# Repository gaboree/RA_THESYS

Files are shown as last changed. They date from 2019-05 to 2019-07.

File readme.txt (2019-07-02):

This directory contains the documentation and software implementation of the Electromechanic rail model digitalization, based on ETCS principles.
The project was realised as Bachelor of Computer Science thesys.

To recreate the project, one needs to understand the documentation, and recreate the hardware components presented there.
With the correct hardware configuration, the code base found here can be used.

Folder: arduino_codes
Contains: implementation of: signal module, acc module, vacancy module, train module
	  tests of: sias algorithm,  register data split algorithm, vacancy module test, simple and duplex serial communication test, signal module test.

Folder: circuits
Contains: the images of the circuit diagrams, and also the source fzz files for each module.

Folder: procesing_codes
Contains: the UI implementation realized in Processing (Java), and the required images for the UI

Folder: document
Contains: the TEX code and used files structure in order to generate the PDF, using a TEX editor, added in zip format too.
	  the generated PDF of the documentation.

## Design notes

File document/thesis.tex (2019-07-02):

%!TeX spellcheck = hu_HU
\documentclass[a4paper,12pt]{article}
\include{preamble}

\author{Gábor Zsolt }
\title{Thesis Computer Science Railway model automated}
\clearcontents

\begin{document}

% Ro Front
\newpage
\pagestyle{empty}
\selectlanguage{romanian}
    \begin{center}
        {\Large Universitatea Sapientia din Cluj-Napoca}\\\vspace{0.07in}
		{\Large Facultatea de Științe Tehnice și Umaniste, Târgu-Mureș}\\\vspace{0.07in}
		{\Large Specializarea Calculatoare}\\
		
		\vspace{2.35in}
		
		{\huge Digitalizare unui model electromecanic }\\\vspace{0.15in}
		{\huge feroviar, bazată pe principii ETCS}
		
		\vspace{0.5in}
		
		{\LARGE Proiect de Diplomă }
		
	\end{center}
	
	\vspace{2.0in}
	
	\begin{multicols}{2}
		\begin{flushleft}
			{\Large Coordonator științific:}
		\end{flushleft}
		\columnbreak
		\begin{flushright}
			{\Large Absolvent:}
		\end{flushright}
	\end{multicols}
	\begin{multicols}{2}
		\begin{flushleft}
			{\LARGE Dr. Székely Sándor Endre}
		\end{flushleft}
		\columnbreak
		\begin{flushright}
			{\LARGE Gábor Zsolt}
		\end{flushright}
	\end{multicols}
	
	\vspace{1.5in}
		
	\begin{center}
		{\LARGE 2019}
	\end{center}
	
\newpage
\includepdf[pages=-]{Detalii_licenta_RO.pdf} 
\newpage
\includepdf[pages=-]{Declaratii_licenta_RO.pdf}
%Romanian abstract
\newpage
\includepdf[pages=-]{turnitin_report.pdf}

\newpage
\pagestyle{empty}
\begin{center}
		{\huge Digitalizare unui model electromecanic }\\\vspace{0.15in}
		{\huge feroviar, bazată pe principii ETCS}
	\vspace{0.1in}
	
    {\LARGE Extras}
\end{center}

Transportul feroviar în zilele noastre e o componentă organică al economiei și al transportului de masă.
Problema principală în tranzitul universal între diferite rețele ferate, este faptul că la nivel de țară sistemul de protecție al trenurilor diferă.
Pentru a soluționa această dificultate, prin UE, sa stabilit ERA (Agenția europeană de transport feroviar) care a dezvoltat sistemul universal ETCS.
Scopul lucrării mele de diplomă este de a integra aceste principii într-un model electromecanic de cale ferată. 
Bazând pe aceste principii sistemul are următoarele proprietăți: e o rețeaua închisă de 3 metrii, compus din căi ferate principale exclusiv, protecție de tren bazat pe un sistem de 8 blocuri, unidirecțional.
Modelul conține o locomotivă electromecanică, în care e integrat un motor de curent continuu pentru propulsie.
Arhitectura sistemului planificat și realizat conține cinci componente principale. 
Fiecare component hardware are în comun placa de dezvoltare Arduino NANO(utilizat pentru control) și modul de radio frecvență NRFL24 tip emisie-recepție (RFC - utilizat pentru transfer date între componente).
Primul, \textbf{controlul de tren}, prin modulare PWM regulează viteza trenului în 3 stări posibile. Semnalul de control vinde de prin RFC de la interfața grafică.
Adițional am instalat și două LEDuri în fața și spatele trenului, care au rol de input pentru sistemul de detectare.
Al doilea, \textbf{rețeaua de detectare}, e construit din 8 foto rezistoare, unul poziționat în fiecare bloc. LEDurile de pe tren activează senzorii și fiind legate de întrările analoage al Arduino, aceasta sunt transmise mai departe la controlul central.
Al treilea, \textbf{rețeaua de semnalizare}, controlează 3 circuite flip-flop pentru a activa o rețea de 8x3 LEDuri. Fiecare bloc are un semnalizator de trei leduri cu aspecte de culoare diferite ( ROȘU - Oprește, Verde - Înaintează, Galben - Atenție/Reduce Viteza).
Al patrulea, \textbf{controlul central}, numit și \textit{interlocking} în industrie, are rol de dealer între componente și garantarea condițiilor de siguranță. 
Pe baza datelor de detectare, prin algoritmul de secvențiere a aspectelor de semnal, determină aspectele de semnalizare de siguranță pentru fiecare bloc. Datele sunt transferate în continuu între el și celelalte componente.
În final, \textbf{interfața grafică}, compus din două părți, unul pentru controlul vitezei trenului, iar celălalt pentru afișarea stării rețelei de detectare și semnalizare. E rulat pe un calculator, și e în contact permanent prin USB, cu controlul central.
Hardwareul a fost programat în Arduino IDE, folosind limbajul C. Interfața a fost realizat cu Processing IDE, folosind limbajul Java.
După construcția și punerea în funcțiune, sistemul a fost testat cu succes cu unu și doi trenuri în rețeaua realizată. Concluzia fiind că e posibil să aplicăm sistemul ETCS pe modele ferate.
Cea mai importantă posibilitate de dezvoltare a sistemului actual ar însemna integrarea unor macaze. Acestea ar permite dezvoltarea rețelei cu căi secundare, și cu gări.
Care la rândul rol sunt condiționate de dezvoltarea controlului prin circulație bi-direcțională în rețea, și implementarea setării traseelor. 

\newpage
\section*{Cuprins}
	\begingroup
	\renewcommand{\section}[2]{}
	\romaniantableofcontents
	\endgroup

%Hungarian tehsys
\newpage
\pagestyle{empty}
\selectlanguage{hungarian}

	\begin{center}
		{\Large Sapientia Erdélyi Magyar Tudomány Egyetem}\\\vspace{0.07in}
		{\Large Marosvásárhelyi Kar}\\\vspace{0.07in}
		{\Large Számítástechnika szak}\\
		
		\vspace{2.35in}
		
		{\huge Elektromechanikus vasút modell }\\\vspace{0.15in}
		{\huge digitalizálása, ETCS elvekre alapozva}
		
		\vspace{0.5in}
		
		{\LARGE Diplomadolgozat}
		
	\end{center}
	
	\vspace{2.0in}
	
	\begin{multicols}{2}
		\begin{flushleft}
			{\Large Témavezető:}
		\end{flushleft}
		\columnbreak
		\begin{flushright}
			{\Large Végzős hallgató:}
		\end{flushright}
	\end{multicols}
	\begin{multicols}{2}
		\begin{flushleft}
			{\LARGE Dr. Székely Sándor Endre}
		\end{flushleft}
		\columnbreak
		\begin{flushright}
			{\LARGE Gábor Zsolt}
		\end{flushright}
	\end{multicols}
	\begin{flushleft}
		{\Large egyetemi adjunktus}
	\end{flushleft}
	\vspace{1.2 in}
		
	\begin{center}
		{\LARGE 2019}
	\end{center}
%Hungarian abstract
\newpage
\pagestyle{empty}
\begin{center}
    {\LARGE Kivonat}
\end{center}
\textbf{Kulcsszavak:} Vasúti modell, ECTS, Vasúti blokk, Jelzö aspektus, Arduino, Rádió frekvenciás kommunikáció.

A vasúti szállítás napjainkban a gazdaság és a tömegszállítás szerves része. Vasúti hálózatok országonként egymástól eltérő vonat védelmi technológiát alkalmaznak, szükségszerűen megalakult, az Európai Unió közvetlen hatására, az ETCS(European Train Control and Signalling). Ez a vasúti hálózatok vezérlésért felelős elvek összessége amelynek célja a vasúti forgalom zökkenőmentes működése ország határokon túl. A diplomamunkám témája, egy egyszerű elektromechanikus modell vasút digitalizálása, az ETCS elveket szem elött tartva. Konkrétan egy ETCS 2-es szintű, fővágányokból álló, zárt, egy irányú, nyílt szakaszú vasúti blokk rendszer szemi automatikus vezérlése. A modell egy három méter hosszú müanyag vágány pályát, és egy DC motorral meghajtótt mozdonyt tartalmazz.A pályát 8 darab vasúti blokkra osztottam.A megvalósított rendszer öt darab fő részre osztható.Mindegyiknek a közös hardver része egy Arduino NANO mikrokontroller (vezérlésért felelős) és egy NRFL24 rádió frekvenciás modul (komponensek közötti kommunikációért felelős). Első a \textbf{mozdony irányítás}. A mikrokontroller PWM modulációval, és egy tranzisztorral kapcsoló üzemmódban, tudja módosítani a mozdony sebességét. Rádió frekvencián keresztül irányítható a grafikus interfészről. Mozdonyra elejére és végére szerelt két LED jelzi az észlelő hálózati szenzornak a mozdony relatív pozícióját. Második az \textbf{ észlelő hálózat} 8 db. fotó-ellenállások által képviselt szenzorok bemenete analóg portokon. A mozdony LED-ekre reagál. Harmadik a \textbf{jelző hálózat} három darab shift regisztert vezérel, amelyek egy 8x3-as LED hálózatot aktiválnak. Mindegyik blokkhoz tartozik egy 3 LED-es jelző amelyek szín aspektusokat állítanak be (Piros - Állj, Sárga - Lassíts és figyelj, Zöld - Szabad a behajtás). Vizuális információ a mozdony vezető számára. Negyedik a \textbf{központi vezérlés} fogadja, feldolgozza, és továbbítja az adatokat a komponensnek között. Szaknyelven egy köztes réteget képvisel amelyet biztosító/óvó rendszernek is neveznek. USB porton keresztül, kapcsolatban van a számítógépen futó grafikus interfésszel. Az interfésztől fogadja a mozdony vezérlési adatokat amelyet továbbit a felelős komponensnek. Végül a \textbf{grafikus interfész} két részből áll. Mozdony vezérlése, három sebesség pozícióval: Állj, Maximális sebesség, Fél sebesség. És a hálózat topológia megjelenítése, a hozzá tartozó észlelési és jelző adatokkal. A rendszerben a komponensek NRFL24-es moduljai egymás között két irányú adat áramlásra képesek. A hardver szintű kód az Ardunio NANO és NRFL24 modul vezérlésére Arduino IDE környezetben íródott C programozási nyelvben. A grafikus interfész Processing fejlesztői környezetben íródott Java programozási nyelvben. A rendszer elkészítése, és összeszerelése után, a rendszert egy valamint két mozdony modullal teszteltem. Az említett rendszer sikeresen teljesítette a dolgozatban megfogalmazott követelményeket. Állíthatom hogy, leskálázott alap szinten, megfelel az ETCS előírásoknak. A rendszer legfontosabb továbbfejlesztési lehetősége a hálózat bővítése vasúti eltérítőkkel. Ez lehetőséget adna állomások, valamint két irányú vágányok integrálására. Az utóbbi pedig a vasúti blokk elv, komplementerére, a vasúti útvonalak megvalósítását tenné lehetővé.
%English abstract
\newpage
\pagestyle{empty}
\begin{center}
    {\LARGE Abstract}
\end{center}
\textbf{Keywords:} Rail model, ETCS, Rail block, Arudino, Radio frequency communication, Signal aspect.

Rail transport in our time is an organic component of the economy and mass transit services. 
The main issue in universal, standardized transit of rail vehicles across all networks, is that each country has adopted his own rules of train protection.
To solve this issue, through the EU, the ERA developed the ETCS (European Train Control and Signaling) set of rules.
This would allow ECTS compliant trains to transit across several ETCS networks belonging to different countries.
The goal of my thesis is to design and implement such a system, using an electro mechanic rail model.
Which will comply with ETCS level 2 rules and has the following properties: it's a 3 meter long loop like closed network, consists of main tracks only, protection based on block system in open line.
The network is broken up in to 8 rail blocks, and the train has a built in DC motor, that must be remote controlled.
So the basic architecture of our system will consist of five main components. In each components case the hardware is built around an Arduino Nano(responsible for control) development board, and a NRFL24 radio transmitter (RTS-responsible for bi-directional data transfer).
First the \textbf{train control} is realized by PWM modulation via the MCU, and the remote control function by the RTS. The input data is coming from a GUI. Additionally two LEDs are installed for train front and rear detection.
Second the \textbf{detection network} consists of 8 photo resistors, that detect the train LEDs, and forward the sensor data to the MCUs analog inputs. Which forwards it to central processing via the RTS.
Third the \textbf{signaling network} drives 3 shift registers, which drive a 8x3 network of LEDs. In each block we have a signal of three LEDs, that represent the speed aspect for the specific block (RED - STOP, GREEN -GO, YELLOW - SLOW).
The data for the activation is coming via RTS from the central component. Fourth \textbf{central control} collects the vacancy data and based on the signal aspect sequencing algorithm, calculates the correct signal aspect for each block. 
This module is considered the central layer, also called interlocking in the industry. Additionally it acts as a dealer, it sends and receives data between the hardware components and the GUI. 
Finally the \textbf{GUI}  consists of a 3 state train control interface and of a rail network state display. 
The hardware level software for the MCU control was written in Arduino IDE, in C language. 
The GUI was developed with Processing IDE, in Java language.
After building and commissioning, the system was successfully tested with one and two trains in the network.
The conclusion being that it is possible to apply ETCS rules on a rail model.
The most significant further development possibility of this system is the integration of point machines, which would allow beside the block system, the implementation of secondary tracks and route setting principle.	
\newpage
\section*{Tartalom}
\selectlanguage{hungarian}
	\begingroup
	\renewcommand{\section}[2]{}
	\tableofcontents
	\endgroup
	\begingroup
	\newpage
	\listoffigures
	\listoftables
	\lstlistoflistings
	\endgroup
\newpage
\pagestyle{fancy}
\rhead{\slshape \leftmark}
%1
\section{Bevezető}\sectionro{Introducere}
\subsection{Bevezető}\subsectionro{Introducere}
A vasúti szállítás volt az első verziója a mechanikus tömeg szállításnak, legyen szó személy vagy árú szállításról. 
A vasút feltalálása meglepően hosszú múltra tekint vissza. A vasút működési alap elvre hasonló szerkezetet, a történészek szerint, az ógörögök már i.e. 600-ban használták. 
A “Diolokos” egy 6-7 km hosszú mészkőből épített pálya volt, és szerepe hajók szállítása volt a Korintusi és a Szaróni öböl között.\cite{jwdrijvers92} 
A hajókat állatokkal húzták át egyik kikötőből a másikban, ezzel jelentősen csökkentve az utazási időt, különben napokban került volna a Peloponészosz félsziget megkerülése.
A következő népszerű vasúti alkalmazás a középkori bányákban használt fa pályákon, lovakkal vontatott, fa szerelvények. Német és angol lakta vidékeken volt gyakran alkalmazva.
Az igazi fordulópont a gőzmotor feltalálása volt az angol James Watt által, majd az ezt követő "gőz szekér" készítése 1804-ben.
A gőzhajtású mozdonyoknak felmérhetetlen szerepe volt a 18-19 században robbanás szerű ipari forradalomnak. Ezt a tendenciát majd később tovább növelte a dízel valamint elektromos motorok megjelenése a 20. században.
A vasút szerepe napjainkban felbecsülhetetlen befolyással bír.Hatalmas mennyiségű személy és árú szállításról ami vasúti hálózatok segítségével bonyolódik le. 
Vincent Baziet francia közgazdász tanulmánya \cite{vbazil13} szerint egy országnak a vasút hálózatának a hatékonysága szoros kapcsolatban áll azzal hogy mennyire fejelt és versenyképes maga az ország gazdasága.

\begin{figure}[htp]
    \centering
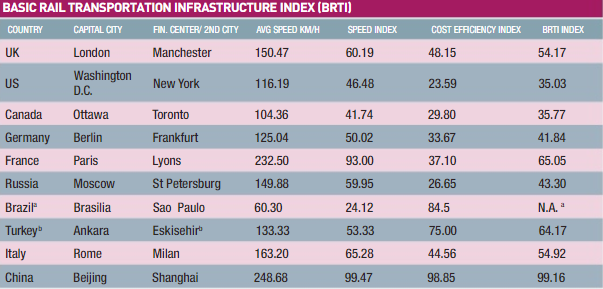
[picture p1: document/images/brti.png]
	
    \caption[Basic Rail Transportation Infrastructure Index]{BRT index}
	\label{fig:brti}
\end{figure}
    
Az általuk kiszámolt BRT index valóban alátámasztotta ezt, amint látható az \ref{fig:brti} ábrán, eredményeiket alátámasztja a stabil fejlődő gazdaságok igen csak magas indexel rendelkeznek.
Látható hogy gyengén fejlesztett vasút hálózatok esetén legtöbbször az index kiszámítása sem lehetséges. 
Tehát a globalizáció korszakában nyilvánvaló hogy a vasúti hálózatok jövője a fejlesztések folytatásával és ezen tudás megosztásával áll szoros kapcsolatban. 

\subsection{A dolgozat témája}\subsectionro{Tematica lucrării}
A dolgozatom témája egy modell vasúti hálózat automatizálásának megvalósítása. Tanulmányozva az iparban használt implementációs elveket, és ahol lehetséges ezekre az elvekre támaszkodva felépíteni a rendszert. Négy fontosabb részre oszthatjuk a rendszerünk amint látható a \ref{fig:realizedsys}. ábrán:
\begin{enumerate}
    \item A központi vezérlés: egy mikrokontroller figyel a hálózatban található többi mikrokontrollere és továbbítja egy számítógépre telepített vezérlő szoftvernek az érkező adatokat. A kommunikáció rádiófrekvencián történik és két irányú.
    \item A mozdony vezérlő: egy mikrokontroller segítségével megvalósítja a mozdonyban található DC motor sebesség vezérlését, valamint parancsokat fogad a központi vezérléstől.
    \item A jelző  hálózat: egy mikrokontroller segítségével megvalósítja a vasút rendszerekben használt jelző lámpák aspektusának a beállítását, a vezérlő adat ugyancsak rádiófrekvencián érkezik a központi vezérléstől.
    \item Az észlelő hálózat:  egy mikrokontroller segítségével megvalósítja a mozgásban levő szerelvény topológiai helyzetét, majd ezt az adatot továbbítja rádiófrekvencián keresztül a központi vezérlésnek.
\end{enumerate}

\begin{figure}[htp]
    \centering
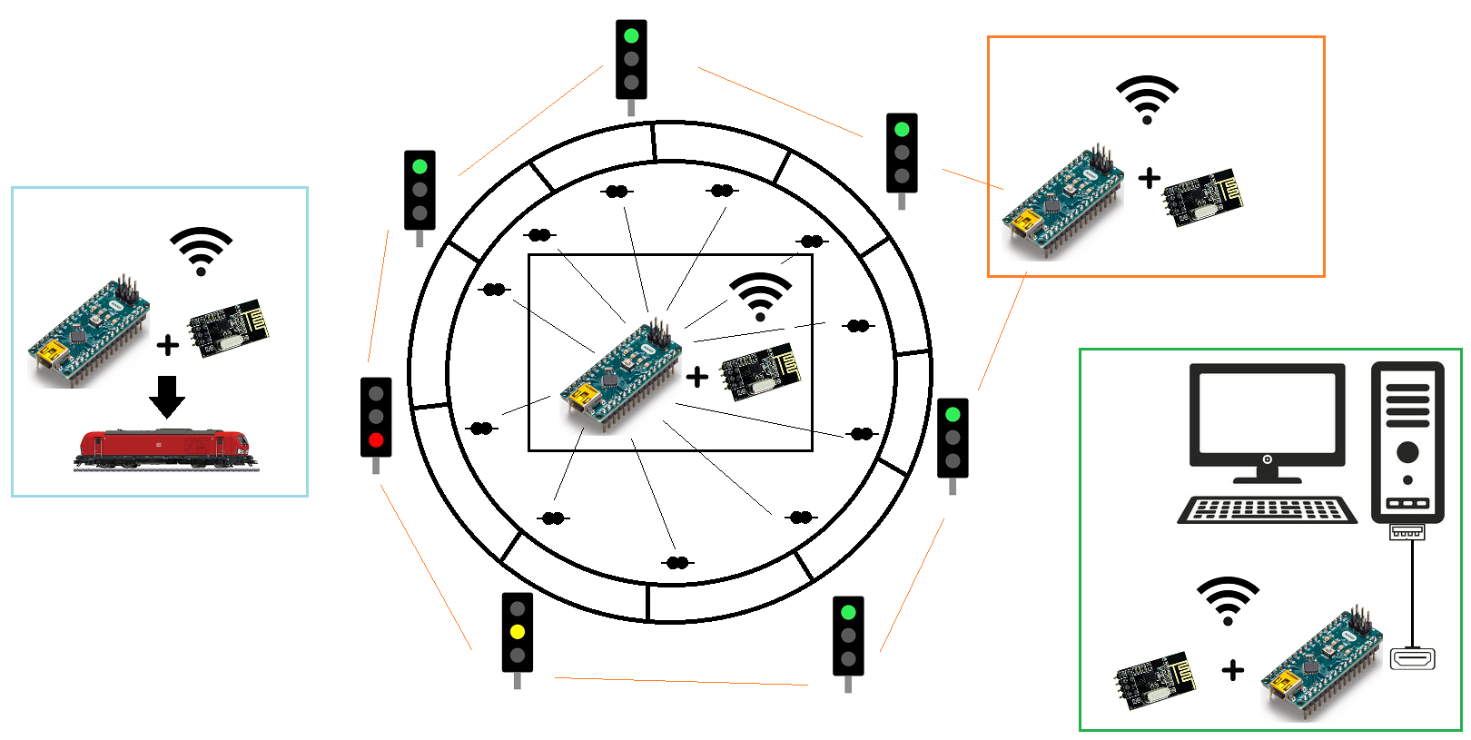
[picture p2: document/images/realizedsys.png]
	
    \caption[Megvalósított rendszer elvi rajz]{Megvalósított rendszer}
	\label{fig:realizedsys}
\end{figure}
%2
\section{Szakirodalmi tanulmány}\sectionro{Studiu bibliografic}\label{RAbasics}

A szakirodalmi tanulmány első sorban egy pár, a szakmában, nélkülözhetetlen könyvre épül.
A \textit {Joern Pachl: A vasúti üzemeltetés és ellenőrzés} \cite{jp09} és a \textit {Gregor Theeg, Sergej Vlasenko: Vasúti jelzés és biztosítóberendezések} \cite{gtsv18}, valamint a \textit{Peter Stanley: ETCS mérnököknek}\cite{ps11} című könyvek szinte kötelező irodalomként vannak számon tartva a vasúti elemek valamint logika fejlesztésének az ágazataiban. 
Értelemszerűen az elkövetkező fejezetek ezen könyvek tartalmának megemésztésével, újra fogalmazásával valamint magyar nyelvre való fordításával készültek el, kiegészítve a szakmában gyakran referált cikkekkel.

\subsection{Vasútrendszerek specifikációi}\subsectionro{Spețificațiile a sistemelor feroviare}
\textit {Jochen Trinckauf} szavait értelmezve az összes vasút rendszer esetében a következő két specifikációt azonosíthatjuk:
\begin{enumerate}
    \item A vonat által követet útvonalat a kerék és a sín mechanikai irányítása határozza meg, és ez az útvonal csak egy kitérő ( speciális vasúti elem) beavatkozásával változhat.
	Ebből kifolyólag lehetőség kell legyen egy ilyen rendszerben az útvonal beállításra, mivel a kitérők több lehetséges útvonalat megvalósítanak. Nyilvánvalóan egy vágányos rendszerek esetén, az irányváltoztatás zárt hurok használatával is megvalósítható. 
    Mivel a jármű szoros kapcsolatban áll az irányító rendszerrel, a vasúti rendszerek lineáris/szekvenciális rendszerekként is azonosíthatóak. 
	\item Az acél alapú vasúti kerekek relatív gyenge fékező képességgel rendelkeznek az ugyancsak acél alapú síneken. 
	Ebből kifolyólag a vezető által látható útvonalon kívül szükség van további elővigyázatossági intézkedésekre, annak érdekében hogy időben tudjon a vezető döntést hozni a sebesség csökkentésére vagy a vágány szakasz elhagyására vagy a teljes megállásra.
\end{enumerate}
\par Tehát ezekből azt a következtetés vonható le hogy, a vasúti rendszerekben esszenciális a helyes jelzés és vezérlés. 
A hálózat menedzser részéről fontos tudnia hogy egy adott időpontban pontosan hol, mikor és meddig van a gördülő állomány.
Annak érdekében hogy tudjon egy optimális és gazdaságos menetrendet szerkeszteni. 
Valamint a mozdony vezető - diszpécser - operátor szemszögéből fontosak ezek az elemek ahhoz hogy biztonságos, elérhető és karbantartott legyen a vasúti rendszer.
\pagebreak
\subsection{Vasúti elvek és standardok}\subsectionro{Principii și standarde feroviare}
Kibővítve a korábbi specifikációkat vasút rendszereknek három fontos részük van:
\begin{itemize}
	\item \underline{Infrastruktúra}, ami magában foglalja a teljes sin hálózatot/pályákat, állomásokat, és az ezekre szerelt mechanikus és/vagy elektromos felszerelést
	\item \underline{Gördülőállomány}, amely a mozdonyok és szerelvényeket képezi, fügétlenül attól hogy közszállítási vagy ipari szállításban használódik
	\item \underline{Üzemeltetési szabályok}, pontosabban a hálózatban használt működési szabályokat és eljárásosakat értjük ez alatt
\end{itemize}
\par Egyszerűség kedvéért az infrastruktúrát és gördülőállományt nevezhetjük a rendszer \textit{hardverének}, valamint az üzemeltetési szabályokat a \textit{szoftverének}.
Egy specifikus alrendszer az úgy nevezett automatikusa vonatvédelmi rendszer (\textbf{Automatic Train Protection}, továbbiakban \textbf{ATP}) felelős az egyik legfontosabb funkcióért a vasúti rendszerekben.
Az ATP szerepe az hogy információt továbbítson az útvonalról a mozdony vezetőhöz és automatikusan megállítsa a mozgó járművet ha emberi mulasztás miatt nem vesz figyelemben egy erre utaló jelzést a központi forgalom irányítótól. 
Ez az alrendszer tehát kapcsolatot teremt a gördülőállomány és az üzemeltetési szabályok között, információt szolgáltatva az infrastruktúrán található egyéb járművekről.
Feltalálása áttörő szerepet játszott a vasúti balesetek csökkentésében és/vagy szinte teljes elkerülésében. Sajnálatos módon az ATP rendszer implementációja nagyon nagy variációnak örvend.
Az európai országok közötti üzemeltetési szabályok annyira különbözőek voltak, hogy a 90-es évek végén több mint 14 különböző nemzeti standardot letehet azonosítani. 
Gyakorlatban szinte minden ország saját szabályokat alkalmaz, ennek az a negatív következménye hogy nagyon megnehezíti az átjárhatóságot az országok között. 
Az Európai Unió megalakulásának és idővel terjedésének köszönhetően, gazdasági okokból szükségszerű lett ezt a problémát megoldani. Mivel rengeteg idő és pénzügyi veszteséggel jár
minden országhatárnál mozdonyokat cserélni vagy készenlétben tartani határon túli szállítmányok esetén. Valamint ugyancsak magas költségel jár egy mozdony felszerelése több ország ilyen rendszerével.
Továbbá a nagy sebességű vonat hálózatok megjelenése, mint például a francia \underline{TGV}, a létező vezérlési technológiát is elavultnak tekintette.
Ezeknek következménye volt az \textbf{ERA - European Rail Agency} vagyis az \textit{Európai Vonat Ügynökség} megalakulása. 
Pár éven belül megalkották az átjárhatóságot lehetővé tevő technikai specifikációt, felkarolva az elődjét az \textbf{ERTMS - European Rail Traffic Management System}-et \textit{(Európai Vasút Forgalom Menedzsment Rendszer)}.
Az ERTMS komponenseként jött létre az \textbf{ETCS - European Train Control System}-et \textit{(Európai Vasút Vezérlési Rendszer)}.
Az ETCS szolgáltatja a technikai megoldásokat legtöbb új fejlesztésű vagy megújításra kerülő vasúti rendszereknek.
Idővel amint a megoldások bizonyították életképességüket,a kivitelezési folyamatot a \textbf{CENELEC} intézmény által standardizálták is.
\subsubsection{ETCS}\subsubsectionro{ETCS}
Az ETCS projekt célja hogy fokozatosan a hagyományos ATP rendszereket Európa szerte egy egységes két irányú kommunikációra képes vonat vezérlő rendszerre cserélje le.
Fontos megjegyezni hogy az újítás mindhárom vasút rendszeri komponenst érinti (Infrastruktúra, Gördülőállomány, Üzemeltetési szabályok).
Az új rendszerben új technológiákat vezettek be mint az \textbf{"euro-balise" (magyarul euró-pályamágnes)} vagy a GSM-R alapú kommunikáció. 
A pályamágnesek szerves részét képzik az ETCS technológiának, lényegében a sínek között elhelyezett jeladó szerkezet. 
Az az amikor egy ETCS rendszerrel felszerelt mozdony halad el fölötte információt továbbit a pályamágnes után következő útvonalról. Nagy előnye hogy statikus adat továbbítás esetén nem igényel külső áramforrást.
A kommunikáció típusától függően több szintre osztották az új megközelítéseket. 
Továbbiakban ezeket nézzük meg közelebbről.

\begin{itemize}
	\item \textit{0 szint} Ez a szint egy átmeneti állapotot ír le, az az eset amikor egy ETCS képes jármú egy non-ETCS hálózatban közlekedik.
	Egy ilyen szcenárióban a gördülőállomány maximum sebesség minimumával halad a hálózatban, és  emellett egy nemzetileg meghatározott 0 szintes sebesség korlátot is be kell tartania.	
	
	\item \textit{1 szint} Ezen a szinten az ATP egy fejlesztett időszakos verzióját találhatjuk és a pályamágnes az integrális fő adat átadási csatorna.
	Lényegében a pályamágnes, az érkező ETCS mozdonynak, mozgás engedélyt és profiladatokat továbbit.A pályamágnes lehet rögzített adat továbbító vagy váltható. 
	Míg az első csak statikus adatot továbbit ( például: földrajzi pozíció), addig  a második legtöbbször egy vonal menti elektromos készülék befolyására dinamikusan megválasztott adatot továbbit ( például: jelző aspektus).
	A pályamágnesek általában csoportokban vannak összekötve, így észlelhető ha valamelyik meghibásodik, valamint a csoport végső tagja képes információt továbbítani a következő csoport első tagjának.
	A csoportok közötti kommunikáció keretantennával bővülhet amely rádió frekvencián képes adatokat továbbítani, ezek az úgy nevezet Euroloop-ok.
	Érezhető hogy így relatív gazdaságosabban nagy távokat le tudnak fedni, lényeges vasút hálózat adatokat szolgáltatva.
	A harmadik lehetséges adat áramlás a helyváltoztatási adat, ezt az észlelő hálózat gyűjti be, az óvórendszer feldolgozza, és megfelelő jelző aspektust állít be, a biztonságos továbbhaladás érdekében.
	A járműn található ETCS berendezés ezen adatok alapján valós időben számol helyzetet, biztonsági féktávot, valamint egy sebességet amit közöl a vezetőnek.
	Ezt az elvi működést láthatjuk a \ref{fig:etcslevel1}. ábrán. Ez az alszinten valósítja meg a  teljes felügyelet módot. 
	Mivel az ETCS rendszer megszakítás nélkül felügyeli az összes befolyásoló paramétert.	
	\begin{figure}[htp]
	    \centering
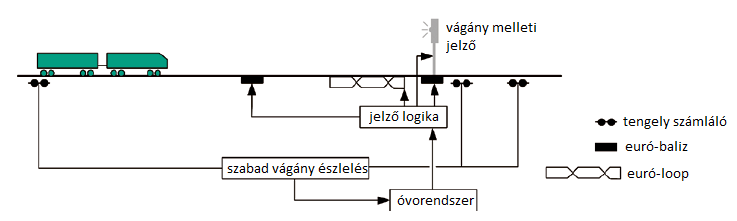
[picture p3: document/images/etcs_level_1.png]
	    
	    \caption[ETCS 1]{Adat folyam ETCS 1 szinten}
	    \label{fig:etcslevel1}
    \end{figure}
	
	Létezik viszont korlátozott felügyeleti mód is. Ez abban az esetben fordulhat elő, ha egy olyan jelző berendezéssel találkozik a jármű amely megállási aspektust mutat a vezetőnek.
	Ilyenkor egyéb ETCS rendszer nem szolgál más adattal, a vezető kénytelen ebben a módban megvárnia az aspektus változást ahhoz hogy tovább haladjon.
	
	\item \textit{2 szint} Egy folytonos ATP rendszerként működik. Ebben az esetben a vonat vezérlő adat GSM-R rádió frekvencián van továbbítva.
	A pályamágnesek továbbra is használtak, viszont döntő többségben statikus adatot szolgáltatnak az áthaladó szerelvénynek, szerepük elektromos vasúti mérföldköre hasonlítható.
	Adott egy adó vevő központ az RBC (Radio Block Center - Rádió Blokk Központ) amelynek a vonat ciklikus idő közönként (általában 60 másodperc) továbbítja a helyzetét meg paramétereit. 
	Válaszként pedig az RBC továbbítja a szükséges továbbhaladási jogokat, valamint egyéb biztonsági paramétereket.
	Vonal menti jelző készülékekre elvileg már nincs szükség csak vonat választási mozgások esetén. 
	Ez esetben a jól bevált észlelő és jelző technológiák használata igényelt, valamint degradált operációs módban szükség lehet erre (pl: non ETCS gördülőállomány hajt be az ETCS hálózatban).
	A \ref{fig:etcslevel2}. ábrán az ETCS 2-es szint egyik lehetséges adatfolyama látható. 
	
	\begin{figure}[htp]
	    \centering
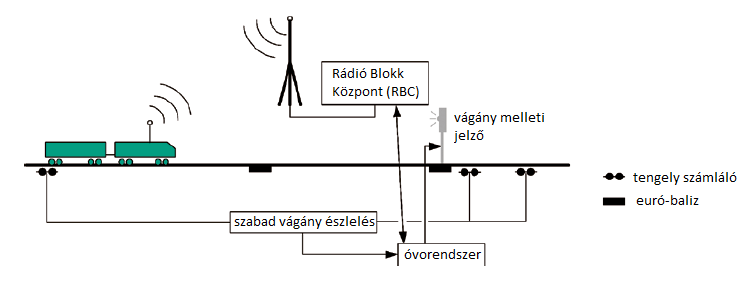
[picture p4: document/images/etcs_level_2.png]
	    
	    \caption[ETCS 2]{Adat folyam ETCS 2 szinten}
	    \label{fig:etcslevel2}
    \end{figure}
    
	\item \textit{3 szint} Végül a \ref{fig:etcslevel3}. ábrán látható adatfolyam jellemző a hármas szintre. Ez esetben bevezetődik a vonat integritás fogalma.
	Hármas szinten garantált kell legyen a gördülőállomány egységessége. 
	Ennek segítségével már elégséges az RBC kommunikáció és pályamágnesek használata, mivel garantáltan tudjuk a jármű hosszát a hálózatban és a hálózat paramétereit.
	Valamint az RBC és jármú közötti kapcsolat folytonos. Ezzel a módszerrel sem észlelő sem jelző berendezésekre nincs már szükség. 
	
	\begin{figure}[htp]
	    \centering
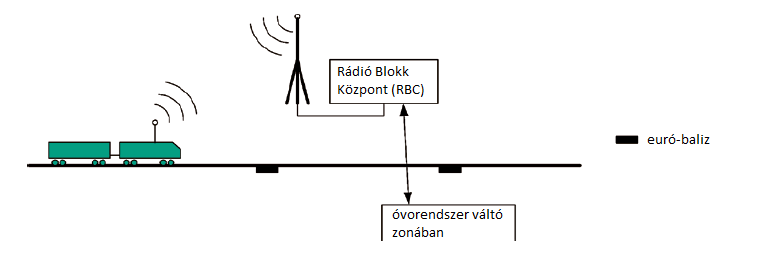
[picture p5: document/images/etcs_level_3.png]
	    
	    \caption[ETCS 3]{Adat folyam ETCS 3 szinten}
	    \label{fig:etcslevel3}
    \end{figure}	
\end{itemize}

Napjainkban döntő többségben ETCS egyes és kettes szintű vasúti projektek vannak használatban vagy kivitelezési folyamatban. 
Az ETCS hármas szintet csak pár regionális ETCS rendszerben tesztelik. Gondot okoz az utóbbinál a vonat integritás kérdése. 
Még nem sikerült egy gazdaságos és standardizálható technikai megoldást találni amely minden körülmény között garantálni tudja a vonat szerelvények egységességét. 

\subsubsection{CENELEC}\subsubsectionro{CENELEC}\label{cenelecchapter}
    \begin{wrapfigure}{r}{0.30\textwidth}
        \vspace{-20pt}
        \centering
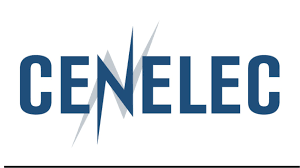
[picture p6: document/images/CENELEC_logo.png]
        
        \caption[CENELEC logo]{CENELEC logo}
        \label{cenelec_logo}
    \end{wrapfigure}

A CENELEC (francia: \textbf{Comité Européen de Normalisation Électrotechnique}) - \textit{Európai Elektrotechnikai Szabványügyi Bizottság} [\ref{cenelec_logo}] egy belga szervezet amely európai standardok megalkotásával foglalkozik az elektromos mérnöki ágazatban. 
Annak ellenére hogy magas mértékben közreműködik az Európai Unió intézményével, nem része ennek.
A különböző ipari és technikai ágazatokban működő uniós ügynökségekkel és magán csoportokkal/konzorciumokkal együttműködve fekteti le az illetékes ágazat európai szintű standardjait.

A vasúti rendszerek kivitelezésében első sorban a biztonságra és kivitelezési folyamatra helyeznek ezen standardok nagy hangsúlyt.

Az EN5012x CENELEC normák érintik a vasúti rendszereket, és a következő standardokat tekinthetjük a legfontosabbaknak:
\begin{itemize}
	\item \textbf{EN 50126} - R.A.M.S. röviden, a vasúti rendszer életciklusát követi különböző szemszögekből, talán a legszervesebb része a vasúti normáknak
	\item \textbf{EN 50128} - A vasúti szoftver alrendszerek életciklusát tárgyalja
	\item \textbf{EN 50129} - Szoros kapcsolatban áll az EN 50126-os normával, további biztonsági folyamatokat szögez le a vasúti jelző rendszerre kitérve, S.I.L.
\end{itemize}

Az EN 50126 norma szerint a vasúti rendszer fejlesztése működtetése/ karbantartása és végül leszerelése egy megtükrözött vízesés módszertanhoz hasonlít.
Amint látható a \ref{fig:cenelec_vmodel}. ábrán ez lényegében a "V" betűre hasonlít, épp ezért is nevezték el V modellnek.

\begin{figure}[htbp]
	\centering
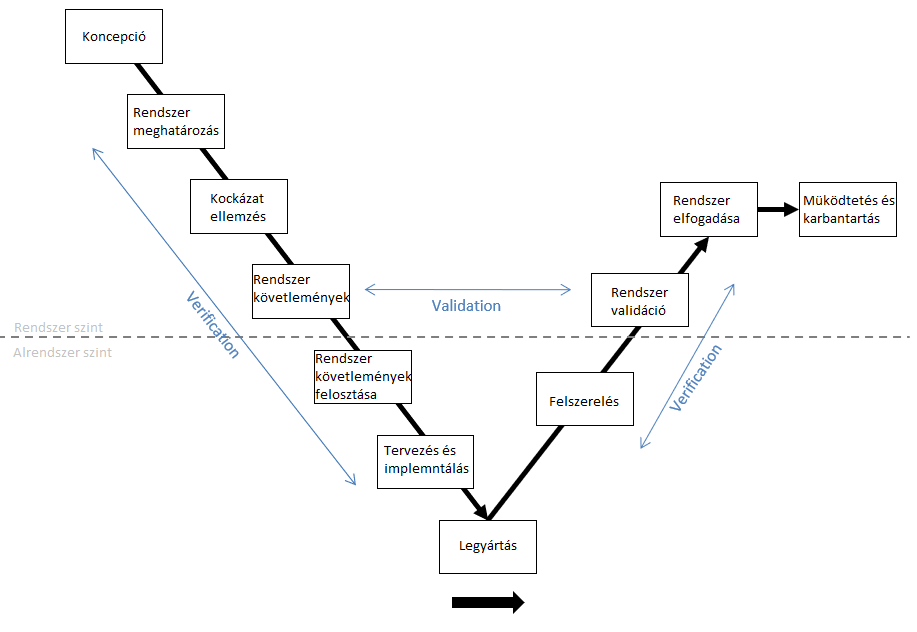
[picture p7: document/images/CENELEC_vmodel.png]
    
    \caption[V modell] {V modell EN 50126 szerint}
    \label{fig:cenelec_vmodel}
\end{figure}

A modell részletes működése és használata nem célja ezen dolgozatnak, éppen ezért nem térünk ki rá bőven. Az rendszer életciklus lépései elég beszédesek ehhez.
Megjegyzendő viszont a verifikáció és validáció fogalma a V modellben. 
Legegyszerűbb értelemben a verifikálási folyamat a \textit{Helyesen építjük ezt a rendszert?} valamint a validációs folyamat a \textit{A kivitelezés megéri? Képes elvégezni a feladatot?} kérdésekre kell megadja a választ.

\begin{wrapfigure}{r}{0.40\textwidth}
    \vspace{-20pt}
    \centering
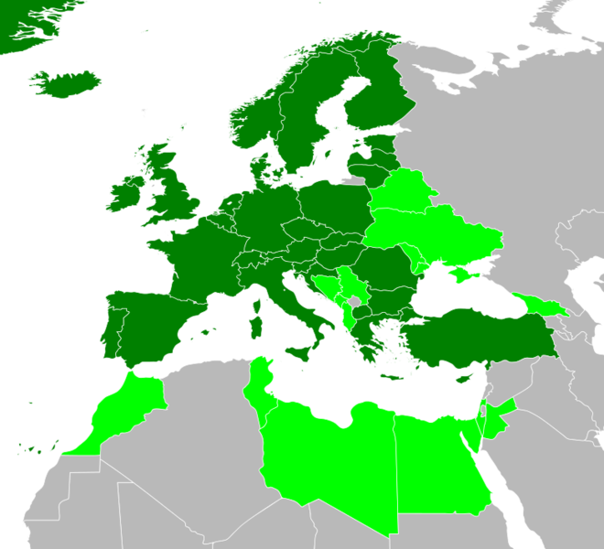
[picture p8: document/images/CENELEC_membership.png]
    
    \caption[CENELEC tagországok]{CENELEC tagországok}
    \label{fig:cenelec_members}
\end{wrapfigure}

Természetesen ezek a standardok nincsenek korlátozva csak európai országokra. 
Amint láthat a \ref{fig:cenelec_members}. ábrán vannak országok amelyek speciális egyezményeket kötöttek és használják saját országaikban is ezeket. 
Ezen túl globálisan is használatban vannak olyan országokban mint Kína, Kanada, Japán, Oroszország, India vagy az Egyesült Államok.

\subsubsection{R.A.M.S.}\subsubsectionro{R.A.M.S.}

Ahogyan a korábbi fejezetekben említettük a vasúti rendszereknek van pár lényeges tulajdonsága. 
A \textbf{R.A.M.S} vagy néha \textbf{R.A.M.S.(S)} rövidítések ezen tulajdonságok összegzése angolul, és jelentése a következő:

\begin{itemize}
	\item {\huge R}\textbf{eliability} -  \textbf{Megbízhatóság}
	\item {\huge A}\textbf{vailability} - \textbf{Elérhetőség}
	\item {\huge M}\textbf{aintainability} - \textbf{Karbantarthatóság}
	\item {\huge S}\textbf{afety} - \textbf{Biztonság}
	\item {\huge S}\textbf{ecurity} - \textbf{Védelem}
\end{itemize}

Fontos leszögezni hogy ezek a fogalmak mit is jelentenek konkrétan vasúti rendszerek kontextusában.
A \textbf{Biztonság} alatt a szó szerinti funkcionális biztonságot értjük, szerepe védelmet nyújtani veszélyes eseményekre. 
Ez lehet technikai hibásodás, de akár nem szándékos emberi hiba is.
A \textbf{Védelem}, ezzel ellentétben , arra szolgál hogy megelőzzön veszélyes következményeket a vasúti rendszere szándékos, észszerűtlen emberi beavatkozás ellen.
A két fogalmat fontos külön értelmezni. Például egy vészkijárat tökéletes analógia erre. 
Ahhoz hogy vészhelyzet esetén használható legyen, az ajtó belülről egyszerűen nyitható kell legyen, tehát zár nélkül. Ez egy biztonsági kérdés.
Viszont ahhoz hogy illetéktelen személy ne tudjon behatolni, ugyanaz az ajtó kívülről zárt kell legyen. Ez egy védelmi kérdés.
Vasúti rendszerekben is hasonló kontextusban értelmezzük ezeket a fogalmakat. Maga a rendszer és ehhez hozzá tartozó komponensek meg kell hogy oldják a biztonság kérdését.
De védelmet is kell biztosítani a rendszeren belül, hogy illetéktelen személyek ne tudjanak hozzá férni és veszélyes eseményeket előidézni.

A megbízhatóság, elérhetőség és karbantarthatóság hatnak egymásra (lásd  \ref{fig:ram_dependency}. ábrát).

\begin{figure}[htp]
	\centering
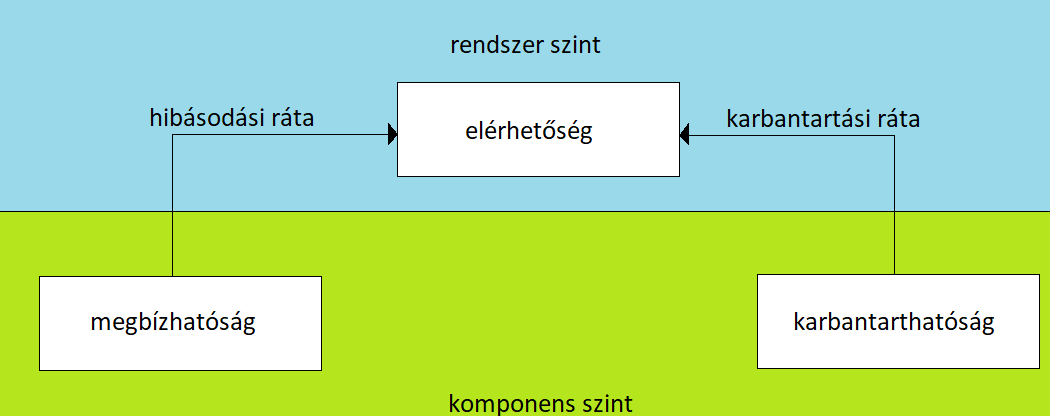
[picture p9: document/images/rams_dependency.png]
    
    \caption[R.A.M. függőség]{R.A.M. függőség}
    \label{fig:ram_dependency}
\end{figure}
\textbf{Elérhetőség} alatt a rendszernek egy olyan képességét értjük amely által képes elvégezni, egy adott időpontban vagy időintervallumban, a neki kiadott feladatot.
Természetesen akkor ha adott a megfelelő keretrendszer ezen feladat elvégzéséhez.
Egy lényeges funkciója a vasúti rendszereknek személyek és árú szállítása biztonságos körülmények között.
Ezért szükségesek előfeltételek, külső segítség források formájában, amelyeknek köszönhetően elvégezheti ezt a feladatot.
Például ez lehet a megbízható technikai komponensek melyek alkotják a rendszert ( óvórendszer, jelző vagy észlelő készülék), de ugyanakkorra mértékben ide tartozik a rendszert működtető személyzet is. 
Tehát a megbízhatóság egy fontos befolyásoló tényezője az elérhetőségnek. 
\textbf{Megbízhatóság} alatt a vasút rendszerben azt a valószínűséget értjük, hogy egy komponens, egy adott időintervallumban, elvégzi a követelmények által meghatározott feladatát.
Ez hiba mentes működéshez vezet. Amikor ez a valószínűség nem jön létre beszélünk hibásodásról, ennek gyakorisága pedig adja meg a hibásodási rátát.
Ezt azt jelenti hogy rendszerünk nem lesz elérhető, ez vezet tehát a karbantarthatósághoz.
\textbf{Karbantarthatóság} is egy valószínűség, amely szerint egy javítási kísérlet egy adott idő intervallumban, kivitelezhető.
Integrális követelmény egy vasútrendszerben a magas elérhetőségi szint. 
Fentiek alapján láthatjuk, hogy ahhoz hogy ez megvalósuljon szükséges a meghibásodási rátát alacsonyan, valamint a karbantartási rátát magasan tartani.

\subsubsection{S.I.L. szintek}\subsubsectionro{Nivele S.I.L.}
Az EN 50129 CENELEC standard egyik fő következménye a veszélyességi ráta leszögezése.
Ez az úgynevezett \textbf{Safety Integrity Level - S.I.L.} vagyis \textit{biztonsági integritás szint} formájában valósul meg.
Egyszerűen fogalmazva elfogadható veszélyességi rátát jelképez, amely függvénye a hibásodások által eredményezett kockáztok csökkentésének, valamint ezek gyakoriságának.
Tehát a vasúti rendszer kockázatoknak van kitéve, ennek pedig két befolyásoló paramétere a súlyosság és a frekvencia vagy előfordulási gyakoriság.
Szükségesé válik ezen kockázatok csökkentése. Ezt új, biztonságosabb technólogikákkal, vagy újabb biztonsági függvények hozzá adásával a rendszerhez, vagy a környezeti tényezők módosításával érhetjük el.
Az említett folyamatok alkalmazásával elérhetünk egy elfogadható kockázat határt.
Ezt a gyakorlatban a CENELEC norma leírja hogy milyen adatok feldolgozásával érhetjük el. 
A tézisnek nem célja hogy ezeket a komplex számításokat elemezzük, épen ezért csak röviden tárgyaljuk a folyamatot.
Az operátor (másképpen a vasúti rendszer megrendelője) kötelező módon végez egy kockázati elemzést, amit a gyártó rendelkezésére bocsájt.
Közösen azonosítják a potenciális veszély tényezőket, ezeket kielemzik és végül, az eredmények alapján, a rendszer különböző komponenseihez biztonsági követelményeket rendelnek.
A minőségi biztonsági követelmények reprezentatívak a S.I.L. szintre tekintve.
A gyártó tapasztalat, tesztek sokasága és statisztikai adatok alapján a rendszer legtöbb altkomponensére azonosít egy lehetséges óránkénti meghibásodás rátát.

\begin{table}[!htbp]
    \centering
    \begin{tabular}{|c|c|}\hline
        THR/óra és fügvény & S.I.L. szint \\ \hline
        $10^{-9} \leq THR < 10^{-8}$ & 4 \\ \hline
        $10^{-8} \leq THR < 10^{-7}$ & 3  \\ \hline
        $10^{-7} \leq THR < 10^{-6}$ & 2 \\ \hline
        $10^{-6} \leq THR < 10^{-5}$ & 1 \\ \hline
    \end{tabular}
    \caption[S.I.L szintek]{THR gyakoriság és a hozzá rendelt S.I.L szintek}
    \label{sil_levels}
\end{table}

Ebből kiindulva számolnak egy elfogadható veszélyességi rátát, amit a szakirodalomban \textbf{THR} ( -  \textit{angol: Tollerable Hazard Rate})-nek neveznek.
Így egy, habár kicsi de mérhető mennyiséggel dolgozhatunk. 
Ezen mérték függvényében 4 S.I.L. szintet határoztak meg, az egyes szint jelképezve a kevesebbe kockázatos elemeket, míg a négyes szint a legkritikusabb befolyással rendelkező komponenseket (\ref{sil_levels}. táblázat).

Például két vonat ütközése egy vonalon katasztrofális eseménynek számít.
Éppen ezért a biztosító rendszer, a jelző rendszer meg az észlelő rendszer pontos és beszámítható működésének kritikus szerepe van egy ilyen esemény elkerülésében. 
Tehát a rendszer ezen komponenseit 4-es szintű S.I.L besorolás alá helyezik. 
De viszont egy autó ütközése vasúti sorompóval, amíg nem kerül a vágányra, habár kockázati tényező nem sodor veszélybe direkt módon emberi életet, ezért ez a komponens csak 1-es szintű besorolás alá kerül.

\subsection{Vasút működtetési elemek és folyamatok}\subsectionro{Elemente și procese de operare a sistemelor feroviare}

A vasúti rendszerek működésének megértéséhez fontos megismerni a rendszer fő \textit{hardver} és \textit{szoftver} komponenseit. 
A \ref{fig:rail_topology_eg}. ábrán egy ilyen rendszer szimbolikus topológiai rajzát láthatjuk a fontosabb komponensekkel. 
A következő alfejezetek ezen szerves komponenseket tárgyaljuk röviden.

\begin{figure}[htp]
	\centering
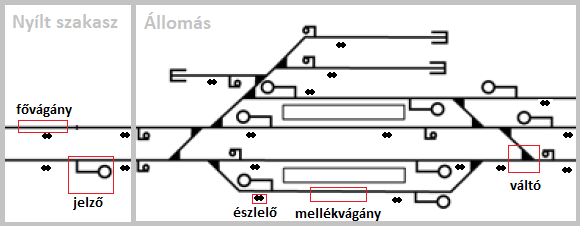
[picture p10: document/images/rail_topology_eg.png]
    
    \caption[Vasúthálózat topológia]{Vasúthálózat topológia és fő komponensei}
    \label{fig:rail_topology_eg}
\end{figure}
Legtöbb esetben a vasúti pályát két jól elkülöníthető  részre oszthatjuk.
Állomásokra és az ezek közötti nyílt szakaszra.

\subsubsection{Vágányok és jelenlét érzékelők}\subsubsectionro{Căi ferate și detectoare de prezență}
A vágány a vasúti hálózatok útteste. Az \ref{fig:rail_track}. ábrán látható struktúra szerint, ballasztra helyezett betonlapokból és sínpárból épül fel.

\begin{wrapfigure}{r}{0.3\textwidth}
	\vspace{-20pt}
	\centering
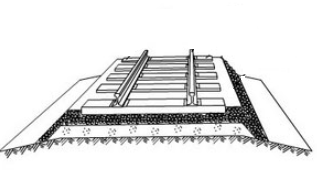
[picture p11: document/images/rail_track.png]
	
	\caption[Vágány struktúra]{Vágány struktúra}
	\label{fig:rail_track}
\end{wrapfigure}

Amint látható a sínpár között van egy jól meghatározót, úgy nevezett, nyomtávolság.
A nyomtávolság standard mérete \textit{1435 mm}, ez annak a következménye hogy a globális vasúthálózat több mint 2/3-a ezt a méretet használja.
Éppen ezért is nevezzük standard méretnek. A vágány és ennek alapja hálózatokban rendezése, eredményezi a vasúti pályák kialakulását.
Alap értelmezetten ez a rendezés a következő típusú elemekből épülhet fel:
\begin{itemize}
	\item \textbf{Fő pálya} - Ez teszi ki a pálya nagy részét, itt haladnak a gördülő állományok jellegzetesen nagyobb sebsebéggel
	\item \textbf{Mellék pálya} - Legtöbbször állomásokon vannak használatban, a járművek speciális mozgásainak elvégzésére, valamint peronok kialakítására is szolgál
	\item \textbf{Kitérő/Váltó} - Mivel a vasúti jármű legtöbbször kényszer pályán halad, szükség van kitérők használatára ahhoz hogy módosítani tudja ezt a pályát.
	A váltószerkezet működtetése kritikus komponens, mivel frontális ütközéshez vezethet helytelen használat esetében. 
	Napjainkban ez a komponens egy elektromechanikus szerkezet, mely minden esetben visszatér eredt állapotában miután az pálya választást lehetővé tette a jármú számára.
	\item \textbf{Kereszteződés} - Olyan esetekben szükséges az implementációja amikor a hálózatban két főpálya keresztezi egymást.
	Jellegzetesen átlósan négy váltó határolja, amelyek párban kapcsolnak garantálva azt hogy egy adott időpontban csak egy vonat haladhat át a kereszteződésen.
\end{itemize}

\begin{figure}[htp]
    \centering
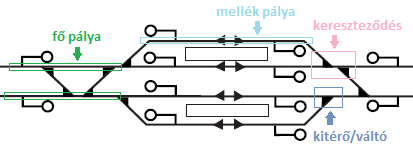
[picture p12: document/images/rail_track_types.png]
    
    \caption[Vasúti pálya komponensek]{Vasúti pálya komponensek}
    \label{fig:rail_track_type}
\end{figure}

A vágánynak egy igen fontos kiegészítő komponense, az ETCS elvek szerint, az úgy nevezett észlelő rendszerek. 
Ezeknek szerepe értesíteni az operátort arról hogy jármű jelenlétet detektáltunk a vágányon. 
Az észlelő rendszereknek funkciói ezen információ észrevétele, továbbítása és feldolgozása.
Ennek két általánosan elterjedt verziója van használatban:
	\begin{figure}[htp]
		\centering
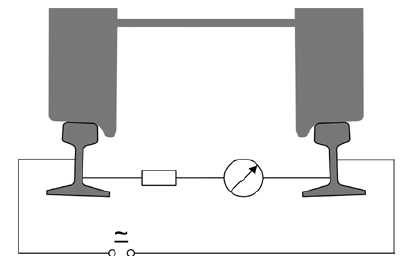
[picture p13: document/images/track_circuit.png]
		
		\caption[Pályaáramkör működési elv]{Pályaáramkör működési elv}
		\label{fig:track_circuit}
	\end{figure}
\begin{itemize}
	\item \textbf{Pályaáramkör} A működési elve a sönt ellenálláséra hasonlít.
	Egy adott pályaszegmens mindegyik sínére egy áramforás egyik egyik pólusát csatlakoztatják. Az áthaladó vonat kerék és tengely páros megnöveli a sönt ellenállást az áramkörben [\ref{fig:track_circuit}].
	Ezt egy szenzor érzékeli és továbbítja az adatot a biztosító rendszernek. Előnye hogy nagyon egyszerű és viszonylag olcsó.
	Viszont van egy kritikus hátránya, ha az áramkör valamilyen okból kifolyólag megszakad vagy az ármarforrás kisebb feszültséget szolgáltat, akkor hibásan jelezhet szabad vonal szegmenst, amikor ez mégis foglalt.
	Ebből kifolyólag ritkán, vagy csak vonat parkoló hálózatokban, használt legtöbbször. Mivel itt kis sebességgel haladnak a járművek, nem kritikus a biztonság.
	
	\item \textbf{Tengely számlálok} A tengely számlálok rezonancia áramkörökre épülnek. A sin mindkét oldalán elhelyeznek egy indukciót generáló adó-vevő rezonancia áramkörpárost [\ref{fig:axle_counter}].
	Ez létrehoz a két áramkör között egy mágneses mezőt. Abban a pillanatban amikor egy szerelvény kerék áthalad ebben a mágneses mezőben, módosul az áramkör induktivitása. 
	Ez a módosulás amplitúdó növekedéshez is vezet a vevő oldalon. Ezt érzékelve, és mivel ugye a kerék a tengelyhez van rögzítve, minden áthaladó tengely egy impulzust fog létre hozni.
	Tehát minden impulzus egy áthaladó tengelyt jelent, ezt az adatot pedig továbbítja a helyszíni feldolgozó egységnek.
	A tengelyszámlálók párban vannak felszerelve a vágány mellet. 
	\begin{figure}[htp]
		\centering
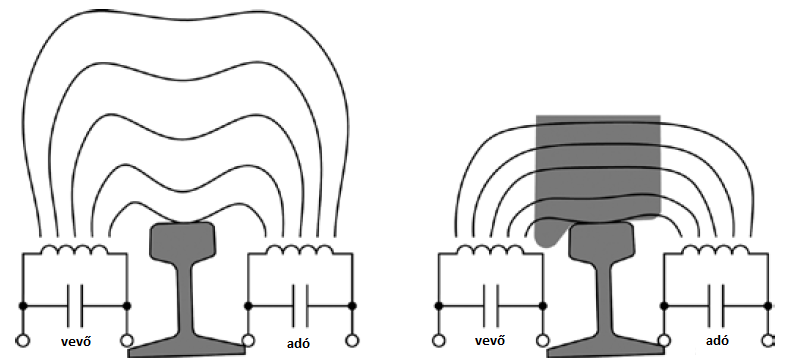
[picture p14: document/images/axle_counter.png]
		
		\caption[Tengely számláló működési elv]{Tengely számláló  működési elv}
		\label{fig:axle_counter}
	\end{figure}
	A számláló pár pedig be van kötve a helyszíni vezérlő áramkörben, amely figyeli hogy az első számláló áramkör ugyanannyi tengelyt számolt mint a második.
	A biztosító rendszerhez csak ennek az összehasonlításnak az eredményét küldi tovább.
	A páros megoldás miatt, a haladási irányt is képes meghatározni.
	Előnyei hogy nem befolyásolják a környezeti tényezők, és hogy irányt is képes érzékelni, valamint nagyon kicsi a hibásodási rátája.
	Viszont komplexebb elektronikai készülékekre van szükség működtetéséhez, amelyek drágábbak mint a pálya áramkörök.
\end{itemize}
A pályaáramkör egy direkt észlelési módszer, mivel a vágányhálózathoz csatlakozik.
Ezzel szemben a tengely számláló indirekt módszer, mivel nem direkt része a vágány hálózatnak. 
Mindkét esetben a cél a vágány foglaltsági állapot pontos meghatározása, és továbbítása a biztosító rendszer felé.
Gyakorlatban többnyire tengelyszámláló fordul elő gyakrabban, mivel pontosabb, kevésbé befolyásolják külső tényezők valamint nem kell a pályát szigetelni a visszáramok miatt.

\subsubsection{Jelzők és jelző aspektus}\subsubsectionro{Semnalizatoare și aspecte de semnal}

A jelző készülékek szerepe az új ETCS megoldások miatt, kezd háttérben szorulni.
Legtöbb ETCS szinten opcionális vagy teljesen szükségtelen. 
Ezek ellenére rendkívüli feladat és hatalmas gazdasági erőfeszítést igényel egy ország teljes hálózatának az átépítése, egy magasabb ETCS szintre.
Gyakorlatban legtöbb esetben hibrid megoldásokat alkalmaznak.
Az az annak ellenére hogy ETCS elv szerint fejlesztik az új hálózatokat, megtartják a jelző készülékek használatát is, főleg állomások és vasúti kereszteződések esetén.

A jelzők szerepe hogy információt továbbítsanak az embereknek, itt első sorban a mozdony vezetőre gondolhatunk. 
De a hálózati menti alkalmazott személyzet számára is fontos lehet.
Ez az információ biztonsági okokból kritikus, mivel a vonatok fix vágányokon mozognak, az ütközés lehetősége igen magas.
Ez a hatalmas tömeg és inerciának köszönhető. Ugyanakkor ennek következménye hogy hirtelen akadály esetén, nehezen képes megállni.
A jelzők a következő fontosabb információkat továbbítják:
\begin{itemize}
	\item mozgási engedély
	\item megengedett sebesség
	\item kitérők helyzete
	\item közelgő vasúti kereszteződés
\end{itemize}

Fizikai korlátozások miatt, a jelző készülékek elhelyezése függ a vonat sebességétől.
Ezt három kategóriában soroljuk:
\begin{table}[!htbp]
    \centering
    \begin{tabular}{ |c|c|c| } \hline
        Pálya típus & Sebesség & Jelző pozíció \\ \hline
        Hagyományos szakasz & $\leq 60 km/h$ & Vágány mentén \\ \hline
        Gyors szakasz & $ \leq 200 km/h $ & Vágány mentén kiegészítéssel \\ \hline
        Magas sebességű szakasz & $ \geq 200 km/h $ & Mozdony kabinban\\ \hline
    \end{tabular}
    \caption[Jelző pozíció és sebesség]{Jelző pozíció és sebesség kapcsolat}
\end{table}
Értelemszerűen nagy sebesség esetén a mozdony vezető már, ha észre is veszi, nem tudom elég gyorsan reagálni az adott jelzésre.
Az ETCS elvek alapján ekkor a jelzés már a vezető rendelkezésre bocsájtott interfészen fog megjelenni.
Közepes sebességek esetén a fő jelző vonalakat kiegészítik távolsági jelző készülékekkel. 
Ennek szerepe hogy értesítse a vezetőt egy közelgő fő jelző állapotáról.
A jelzők legfontosabb biztonsági paramétere az aspektus. Ami nem jelent mást mint a jelző által kibocsájtott fény színéhez rendelt mozgás típus.
Ezt tekintően országonként változhat a segéd jelzések típusa és értelmezése.
Viszont a fő elv, az ETCS-nek megfelelően is, a \ref{tab:aspectandcolor}. táblázat szerinti értelmezést írja elő globálisan.

\begin{table}[!htbp]
    \centering
	\begin{tabular}{ |c|c| } \hline
		Szín & Aspektus \\ \hline
		fehér \cellcolor{white} & Tolatás \\ \hline
		piros \cellcolor{red} & Stop \\ \hline
		zöld \cellcolor{green} & Szabad \\ \hline
		sárga \cellcolor{yellow} & Figyelem \\ \hline
	\end{tabular}
	\caption[Jelzőszín és aspektus reláció]{Jelzőszín és aspektus reláció}
	\label{tab:aspectandcolor}
\end{table}
A jelző berendezés is alárendelt a szokásos ETCS és CENELEC biztonsági protokolloknak.
Ami ezt jelenti hogy kritikus befolyásoló jellege van, kommunikál a biztosító rendszerrel valamint az operátor interfésszel.

\begin{figure}[htp]
	\centering
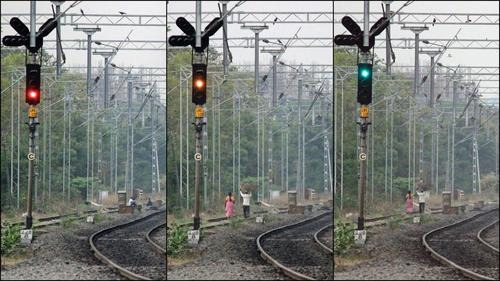
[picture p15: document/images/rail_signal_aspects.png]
	
	\caption[Jelző készülék]{Standard vasúti jelző készülék működés közben az alap aspektusokkal}
\end{figure}

\subsubsection{Vonat mozgások}\subsubsectionro{Tipuri de deplasare a trenurilor}
A vonatok áthaladását a vasúthálózaton, egy menetrendre alapuló, specifikus szegmensekre behajtási engedéllyel rendelkező utasítások sorozata.
A menetrend egy olyan beosztást is tartalmaz, amely az engedély mellet tartalmazza a bizonyos szegmens sebesség korlátozását is.
A vonatok, biztonsági okokból, hátsó lámpával vagy táblával is fel vannak szerelve.
Ezúton ellenőrzik sok esetben a szerelvény sorozat integritását.
A vonatmozgásokat két kategóriában soroljuk:
\begin{enumerate}
	\item \textbf{Normál vonat mozgás} - Az összes, állomáson kívüli, fő pályán történő mozgás ilyen típusú. 
	\item \textbf{Tolató mozgás} - Azon mozgások mely során a vonat vágányt vagy irányt cserél vagy szerelvényekkel bővül/csökken.
	Legtöbbször állomás területén belül történik, mellékpályákon, váltók és kereszteződések segítségével.
\end{enumerate}
Továbbá fontos megemlíteni a behajtási engedély forrását. 
Első sorban, jelzők által irányított pályán, ez a biztosító rendszer által szolgált jelző aspektus adja.
Ha \textit{STOP} aspektust mutat a jelző, a vonat tovább hajthat de csak abban az esetben ha felügyelő operátor verbálisan vagy írásban engedélyt ad erre.
Másod sorban ha nem jelzők által irányított pályán halad akkor a menetrend és operátor utasításai alapján történik a tovább haladás.

\subsection{Biztosító rendszerek}\subsectionro{Sisteme de cuplare/asigurare}
Ahogyan a korábbi fejeztek is referálták a \textbf{biztosító rendszer} ( \textbf{en: Interlocking}) egy kritikus része a vasúti rendszerek architektúrájának.
Lényegégben egy köztes szoftver réteg a vágány mellet készülékek és az operátor interfésze között.
Képes garantálni hogy az észlelő szenzorok által szolgált információ alapján, a jelző hálózat komponenseit egy szekvenciális és konfliktus mentes állapotban beállítva, biztosítja a hálózatbeli vonat mozgásokat.

\begin{figure}[htp]
	\centering
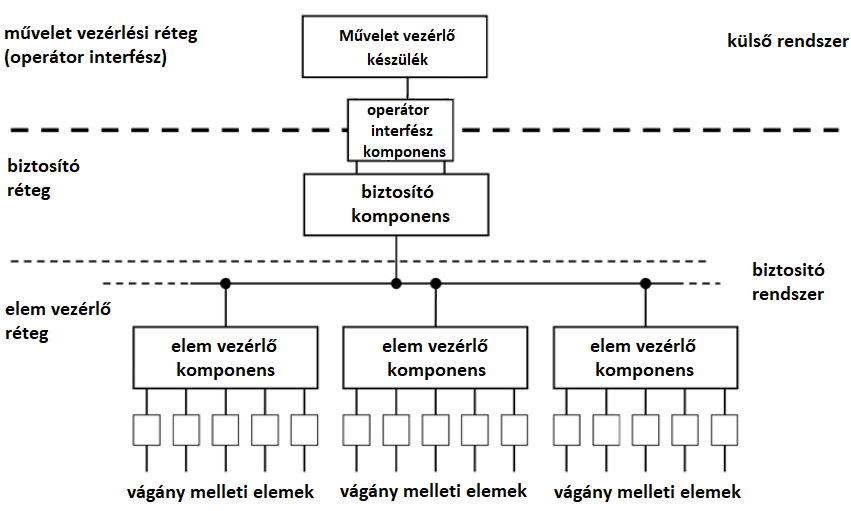
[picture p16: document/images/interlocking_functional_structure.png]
	
	\caption[Intrlocking funkcionális struktúra]{Elektromos biztosító rendszer funkcionális struktúrája}
	\label{fig:interlocking_functional_structure}
\end{figure}

Struktúrája a következő rétegekre osztható [\ref{fig:interlocking_functional_structure}. ábra]:
\begin{itemize}
	\item \textbf{Művelet vezérlési réteg} \\
	Konkréten ez egy külső szerkezet, távirányítással valósul meg a kommunikáció a biztosító réteggel, mivel legtöbbször az operátor interfész nagyon távol van a vágány menti vezérléstől.
	Gyakorlatilag nem a biztosító rendszerhez tartozik, viszont interfészeken keresztül két irányú kommunikáció valósul meg a két réteg között.
	Ezért is funkcionális megközelítésből egyként tárgyaljuk őket.
	\item \textbf{Biztosító réteg} és \textbf{elem vezérlő réteg} \\
	Ezek a rétegegek képezik a biztosító rendszer szerves részét.
	Konkrétan a a biztosító rétegben valósulnak meg az előírt biztonsági és biztosító funkcionalitások mint a folytonos adat továbbítás, vágány menti szenzor értékek kiértékelése vagy a jelző aspektus számítások.
	Az elem vezérlő komponens rétegben pedig az elsődleges hardver közeli állapotok beolvasása és a korábbi réteg rendelkezésére bocsájtása játszódik le. 
\end{itemize}

Az iparban több biztosító rendszer implementáció is létezik, viszont nagy vonalakban mindegyik ez a funkcionális architektúra alapján épül fel.

\subsubsection{Blokk elv és függősségek}\subsubsectionro{Principiul și dependențe de bloc}
Fontos megismerni azon elvet és szabályokat amely alapján a modern biztosító rendszerek a vágány menti szenzor adatokat kiértékelik, valamint a jelző aspektusokat meghatározzák.
Ennek két formája tágan alkalmazott az iparban. 
Az egyik az útvonal foglalás a hálózatban, ez főleg olyan pálya szakaszokon alkalmazott ahol eltérítő készülékek is vannak.
Legtöbbször ez egy állomás területén fordul elő.
A másik a \textbf{blokk elv} segítségével biztonságos és hatékonyan érhetjük ezt el megakadályozva a vonatok ütközését, vonal szerű szakaszokon ahol nem fordulhat elő eltérítő.
Gyakorlatban ez a két elv kombinációját alkalmazzák, almásokban útvonal foglalás történik míg ezek között blokk elvet.
Mivel ezen tézisnek nem célja az útvonal foglalás tanulmányozása, a blokk elvet fogjuk közelebbről megvizsgálni [pl: \ref{fig:automatic_block}. ábra].

\begin{figure}[htp]
	\centering
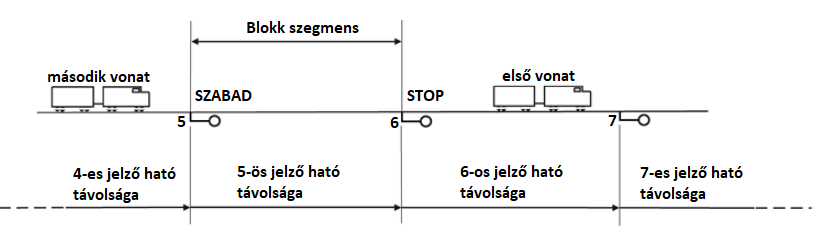
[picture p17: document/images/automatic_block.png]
	
	\caption[Automata blokk]{Egyszerű automata blokk elvi rajza}
	\label{fig:automatic_block}
\end{figure}

Az alap elv az hogy a vonal szegmenseket alrészekre osztjuk fel, azaz blokk egymást követő sorozatára.
Az ehhez tartozó fő szabály pedig az hogy egy blokkban egy időben csak egyetlen vonat tartózkodhat.
A blokkok közötti kommunikációt pedig a jelző hálózat biztosítja.
Tehát a blokk mind két végén kell lennie egy jelző készüléknek amelyek aspektusa módosul amint a vonat elérte ezt a pontot.
Valamint a blokkban kell lennie egy észlelő készüléknek amely garantálni tudja azt hogy egy jármű elhagyta a blokkot.
Továbbá a mérete akkorra kell legyen hogy \textit{STOP} aspektussal találkozva a vonatnak létezzen egy biztonságos megállási távolság.

A blokk elv viszonylag régi múltra tekint vissza, és tág értelemben kronológiailag a következő típusai léteznek:
\begin{enumerate}
	\item \textbf{Kézi blokk}\\
	Ez volt a kezdeti formája, konkrétan a vezető amint elért egy jelző készüléket a vonalon manuálisan kellet beállítsa a készüléket ahhoz hogy a következő érkező vonat tudja hogy foglalt a következő blokk.
	Emellett különböző folyamatokkal értesítették(pl. telefon segítségével) egymást és az operátort a blokk állapotáról, de első sorban a menetrend alapján váltogatták a jelzők aspektusát.
	Ez ahhoz vezettet hogy ha valamelyik vonat valamilyen okból kifolyólag késet, akkor az összes követő vonat is késést szenvedett. Ez egy nagyon nem hatékony hálózat kihasználtsághoz vezet.
	Pár helyen napjainkban is alkalmazzák ezt az elvet, viszont a következő elv kifejlesztésének következménye képen elavulóban van.
	Ennek megfelelője az ETCS 0 szint amely többnyire látás alapú behatolást engedélyez ehhez hasonló pályákon.
	\item \textbf{Automatikus blokk}\\
	Két tényező váltotta ki az automatikus blokk kifejlesztését és tág körű használatát.
	Az első az volt hogy, a késés tényezőn kívül, a kézi blokk rengeteg emberi erőforrást igényelt, és ebből következően több emberi hibához is vezethetett, ami amint eddig is láthattuk katasztrofális következményekkel járhat.
	A másik pedig a technológia fejlődése, és a modern észlelő rendszerek, meg jelzők, megjelenése volt.
	Kikerülve a kézi megoldást, így nagyon felgyorsul az egymást követő vonatok gyakorisága. Ami a hálózat magasabb szintű kihasználásához, valamint a vonatok gyakrabb és pontosabb menetrendjéhez vezet.
	Tehát ez az elv bevezetése költségek csökkentését és a vasút hálózat kapacitásának a megnövelését eredményezte. 
	Legtöbb automata blokk rendszer, három vagy négy blokkos lefedést alkalmaz. Tehát ha egy jármű található az első blokkban akkor a biztosító rendszer automatikusan megtiltja a behajtást, valamint figyelmeztető jelzést állít be a második blokkban.
	Végül a harmadik blokkban normális behajtást engedélyez. Ez e lefedés sűrűn átjárt hálózatok esetén állhat négy vagy több blokkból, megnövelve a biztonsági tényezőt.
	Megfelelője részleg az ETCS 1-2 szintje.
	\item \textbf{Mozgó blokk}\\
	A mozgó blokk gyakorlatilag tükrözi az egész elvet. A blokk már nem egy pálya szegmenst képvisel, hanem minden vonat kibővítve egy biztonsági távolsággal előtte és mögötte, képez egy blokkot.
	Tovább lépve szükséges tudni a hálózatban az összes vonat helyzetét és sebességét, valamint mindegyik folytonos kommunikációs kapcsolatban kell legyen egy központi vezérlő fennhatósággal.
	Ez az elv alapján lehetne maximalizálni a hálózat kapacitást. Mivel így a vonatok a lehető legközelebb tudnak egymáshoz képest átjárni a hálózaton, betartva a biztonsági protokollokat.
	Ennek a teljes megfelelője az ETCS 3-as szint, amely napjainkban még fejlesztés alatt áll. Közjáratokon még nincs implementálva ehhez hasonló rendszer.	
\end{enumerate}

Összegezve elmondható hogy napjaikban az automata blokk elv örvend a legnagyobb népszerűségnek. 
Amely az alkomponenseket egy blokkba zárva automatikusan meghatározza a vonat hálózat blokkjaiban a behajtási engedélyt.
Továbbá az automata blokk egyirányú mozgást feltételez.

\newpage
%3
\section{Elméleti megalapozás}\sectionro{Baze teoretice}\label{theory_section}

\subsection{Pequetren vasút modell}\subsectionro{Model de cale ferată Pequetren} \label{sec:ptmodell}
A tervezett vasúti rendszer kiinduló pontját képzi a \textit{Pequetren} gyártó \textbf{J34167} azonosítóval rendelkező terméke [\ref{fig:peque_tren}].
Ez egy, a vasút modell gyártók standard skálái szerint, HO kategóriás modell.
A HO kategória számszerűen 1:87-es skálázást jelent.

\begin{figure}[htp]
	\centering
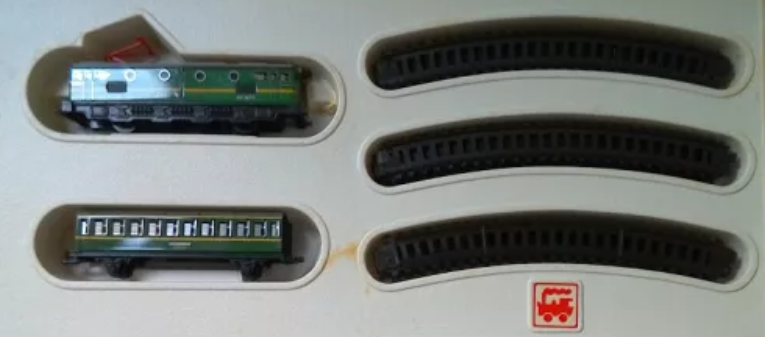
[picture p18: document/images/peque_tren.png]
	
	\caption[Vasút modell]{A modell, amelyre a rendszerünk épül}
	\label{fig:peque_tren}
\end{figure}

Ez a termék egy mozdony és vágányokat tartalmazz.
Pontosabban 12 darab, egyenként 24 centiméter hosszú és 1,6 centiméter szélles, enyhén görbíttet vágányt. 
Vagyis egy 2,9 méter hosszú kör alakú pálya megépítésére alkalmas.

A jármű pedig egy 16 centiméter hosszú mozdony. 
Ez a mozdony gyári előírás szerint egy 3 Voltos elem telepet igényel a meghajtáshoz.
A működésben hozása nagyon egyszerű, két darab 1,5 V-os elemet helyezve a kijelölt foglalatban és a rendelkezésre bocsájtott kapcsolóval zárva az egyszerű áramkört, a motor folyamatosan hajtja a kerekeket.
Pontosabban egy egyen áramú motor tengelye, mechanikus áttétel, hajtja a mozdony hátsó kerekeit.

Fontos megemlíteni hogy a termék semmilyen egyéb áramkörrel nem rendelkezik amely az automatizálási folyamatot segítené.

Mivel a gyártó csak ennyi információt bocsájt a rendelkezésünkre, a tervezés fejezetben bővebben kitérünk még a motor vezérlésére.

\subsection{Vezérlés - Arduino NANO}\subsectionro{Control - Arduino NANO}\label{sec:arduinonano}
Az \textbf{Arduino NANO} [\ref{fig:arduino_nano_overview}. ábra] egy olyan multifunkcionális kis méretű fejlesztői lap amely a 8 bites ATmega328P, AVR családban tartozó, mikróvezérlő körül épül.
Sajátos tervezése és méretének köszönhetően, viszonylag egyszerűen beépíthető legtöbb mikróvezérlő centrikus projektben.

\begin{figure}[htp]
    \centering
    \begin{minipage}{0.45\textwidth}
        \centering
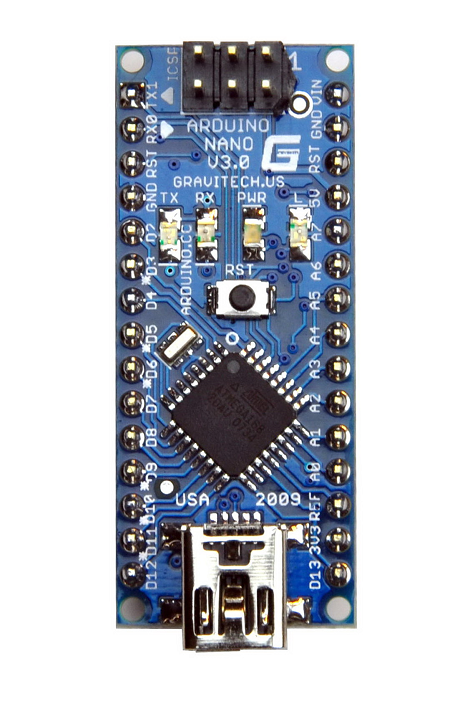
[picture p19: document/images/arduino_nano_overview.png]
        
        \caption[Arduino Nano felülnézet]{Arduino Nano felülnézet}
		\label{fig:arduino_nano_overview}
    \end{minipage}\hfill
    \begin{minipage}{0.45\textwidth}
        \centering
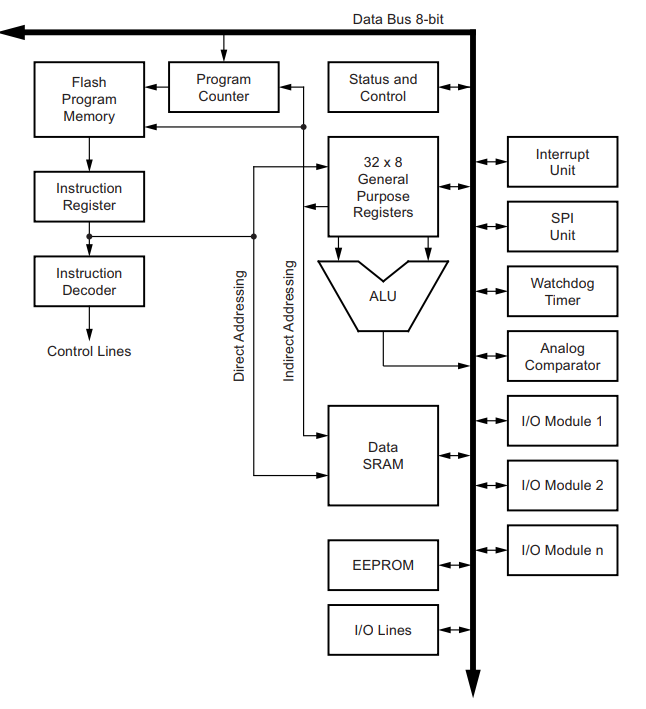
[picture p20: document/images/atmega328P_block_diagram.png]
        
        \caption[ATmega328P blokk diagram]{ATmega328P blokk diagram}
		\label{fig:atmega328P_block_diagram}
    \end{minipage}
\end{figure}

\subsubsection{ATmega328P MCU struktúrája}\subsubsectionro{Structura MCU-ului ATmega328P}

Az \textbf{ATmega328P} egy kis fogyasztású, 8 bit-es, CMOS mikróvezérlő. 
A mikróvezérlő az AVR gyártó által fejlesztett RISC architektúrájára  épül \textbf{Reduced Instruction Set Computer}. 
Maga a RISC architektúra a Harvard architektúra leszármazottja.
Ennek az elve lényegében az hogy a mikroprocesszor egy kis méretű, nagyon optimizált, utasítás készletet használ.
Ezen architektúra alternatívája az úgy nevezett von Neumann architektúra, amely komplex utasítás készletet használ.
Annak ellenére hogy a RISC alapján több utasítást kell a processzor elvégezzen, ezek végrehajtása csak egy órajelnyi időt igényelnek. 
A "redukált utasítás készlet" pedig kevesebb tranzisztor igényel a tároló helyen (CISC-hez képest) így több hely marad általános célú regisztereknek. \cite{er00}
Felbontva kisebb utasításokra a munkát a tároló regisztereket nem szükséges kitörölni, mint a CISC-nél.
A jól meghatározott teljesítmény egyenlet alapján látható, hogy míg a CISC megközelítés az \textit{utasítás} paramétert, addig a RISC a \textit{ciklust}, pontosabban a \textit{ciklus/utasítás} csökkentésével éri el ugyanazt az eredményt:
\begin{equation*}
\frac{\text{idő}}{program} = \frac{\text{idő}}{ciklus} \times \frac{ciklus}{\text{utasítás}} \times \frac{\text{utasítás}}{program}
\end{equation*}
A \ref{fig:atmega328P_block_diagram}. ábrán bemutatott ATmega328P blokk diagramján láthatjuk a RISC architektúra alapú mikróvezérlő blokk diagramját.
A mikróvezérlő adatlapjából pedig a következő képességeket olvashatjuk ki \cite{avratm15}.
Az aritmetikai logikai egység \textbf{(en: ALU) }végzi el az utasításokat, betöltve a 32x8-as regiszterekben az operáció bemeneteit valamint eredményeit.
Az ATmega328P 131 utasítást tartalmazz az utasítás regiszterben. Egy 16 MHz-es oszcillátor kristály biztosítja a másodpercenkénti óraciklus gyakoriságát.
Az írt programot feltölthetjük a 32 KByte-os flash memóriában. Továbbá belső használatra tartalmazz 1 KByte EEPROM, valamint 2 KByte SRAM memóriát.
Végül pedig egy szélles skálájú periferikus funkciókkal rendelkezik:

\begin{itemize}
	\item Két 8 valamint egy 16 bites időzítő/számláló
	\item 6 PWM csatorna
	\item 8 10 bites ADC csatorna
	\item Programozható soros USART interfész
	\item Mester/szolga soros SPI interfész
	\item I2C interfész
	\item Analóg komparátor
	\item Megszakítási és felébresztő bemenetek
\end{itemize}

Mivel a fejlesztő lapnak köszönhetően a felprogramozás, regiszterek kezelése, valamint időzítés automatikusan kezelve van, ennél bővebben nem szükséges az mikróvezérlő működését tanulmányozni.
A többi használt funkcionalitást pedig a következő fejezetben részletezzük.

\subsubsection{Arduino NANO funkciói}\subsubsectionro{Funcțiile al Arduino NANO}
Az Arduino fejlesztő lapok az \textit{arduino.cc} vállalkozás nyílt forráskódú szoftver és hardver terméke.
Egyszerűsített félépítése és programozhatósága miatt rendkívüli népszerűségnek örvend.
A Nano az egyik legkisebb méretű ilyen fejlesztő lap, amelynek a központjában a korábban említett ATmega328P mikróvezérlő áll.
A mikróvezérlőt kibővítettek még pár funkcionalitással amely megkönnyíti akár a hétköznapi felhasználó számára is a használatot.
Ennek ellenére a nagyon kompetens mikróvezérlőnek köszönhetően a legtöbb beágyazott vagy IOT rendszer központi pillére lehet.

\begin{table}[!htbp]
    \centering
    \begin{tabular}{|c|c|c|}\hline
        Kivezetés szám & Fő szerep & Másodlagos szerep\\ \hline
        D0 - D13 & Digitális ki/be menet &  \\ \hline
		A0 - A7 & Analóg be menet & Digitális ki/be menet \\ \hline
        D0 (RX) és D1 (TX)  & & Soros kommunikáció \\ \hline
        D3, D5, D6, D9, D11 & & PWM képes \\ \hline
		A4, A5 &  & I2C kommunikáció \\ \hline
		D10, D11, D12, D13 &  & SPI kommunikáció \\ \hline
		D13 &  & Állapot led\\ \hline
		D2, D3 &  & Külső megszakítás \\ \hline
    \end{tabular}
    \caption[Arduino Nano pin beosztás]{Arduino Nano kivezetés beosztás}
    \label{tab:arduino_pint_out}
\end{table}

A \ref{tab:arduino_pint_out}. táblázatban található kivezetés beosztáshoz, láthatóan több funkció is tartozhat \cite{adaq18}:

\begin{itemize}
	\item \textbf{Digitális ki/be menet}
	Alapvetően ebben a módban a kivezetés digitális logikai igen vagy nemet olvas vagy ír.
	Azaz \textit{+5V } az a logika IGEN (\textbf{HIGH}) és a \textit{0V} a logikai nem (\textbf{LOW}).
	\item \textbf{Analóg be menet}
	Ezek a bemenetek képesek \textit{0V - 5V} tartományban észlelni feszültséget.
	Az így beolvasott értéket egy ADC áramkör átalakítja digitálisan értelmezhető jelre.
	Az Arduinoban található ADC 10 bites felbontásra képes. 
	Ez az jelenti hogy az említett feszültség intervallumot $2^{10} = 1024$ részre ossza fel, arányosan az észlelt feszültséggel.
	Operációs módtól függően az analóg bemenetek konfigurálhatóak digitális ki/be menetekként is.
	\item \textbf{Soros kommunikáció}
	A fejlesztőlap a D0 és D1 kivezetések segítségével képes soros kommunikációt megvalósítani más mikróvezérlőkkel vagy más soros kommunikációra képes készülékkel, pl. számítógép.
	Az Arduino NANO esetében ez a két port egy B típusú mini USB porta van bekötve.
	Amikor aktív a kommunikáció a D0 RX és a D1 TX módba áll.
	RX az adat fogadást képviseli(\textit{en: Receive}), TX pedig az adat küldést (\textit{en: Transfer}).
	Ezt a kommunikációt az ATmega328P USART (\textit{en: Universal Synchronous/Asynchronous Receiver/Transmitter}) csipje valósítja meg felhasználva a standard RS-232C kommunikációs protokollt.
	Ebből következően a kommunikáció létrehozható szinkron és aszinkron módban is. 
	Röviden szinkron módban nagyobb adatmennyiséget tudunk egyidőben továbbítani több sorosan csatlakozott készüléknek.	
	\item \textbf{Impulzus szélesség moduláció képes}
	A D3, D5, D6, D9 és D11 portok PWM képesek. Ez azt jelenti hogy képesek digitális jeleket analóg formában önteni.
	A PWM egy modulációs technika amelynek két fontos paramétere van: az aktív ciklus idő és a frekvencia.
	A frekvencia megadja hogy mennyi idő szükséges egy ciklus teljes befejezéséhez, és hogy milyen gyorsan vált a digitális jel a HIGH és LOW értékek között.
	Az aktív ciklus idő legtöbbször százalékosan van jelenítve. A lap egy 8 bites PWM kimenetre képes, tehát $2^{8} = 256$ felbontásban tudjuk ezt irányítani.
	Konkréten ha az aktív ciklus 100(\%) akkor a kimeneten folytonos 5V fog megjelenni, ezt ha csökkentjük például 75(\%)-ra akkor $5V \times 0.75 = 3,75 V$-t tudunk kialakítani.
	\item \textbf{$I^{2}C$ kommunikáció}
	Az A4 és A5 port másodlagos szerepében az $I^{2}C$ kommunikációra képes. 
	Ez egy szinkron multi-mester multi-szolga kapcsolatot képes létrehozni ugyancsak soros kapcsolatra épülve.
	\item \textbf{SPI kommunikáció}
	Soros periféria interfészt használva egy következő szenzorlapot vagy mikróvezérlőt köthetünk össze a saját lapunkkal. 
	A létrejött kapcsolat ugyancsak egy soros kommunikációt valósít meg, egy mester- egy vagy több szolga adat buszt képezve.
	Itt az említett portoknak fontos szerepe van amelyet nem lehet figyelmen kívül hagyni konfiguráció közben:
		\begin{itemize}
			\item D10 - \textit{SS - Slave Select}
			Meghatározza hogy a mester melyik szolga készülékkel kommunikáljon.
			\item D11 - \textit{MOSI - Master Out Slave In}
			A mester adat vonala, amelyen küldi az adatot a periferikus szolgának.
			\item D12 - \textit{MISO - Master In Slave Out}
			A szolgák adat vonala, amelyen adatot küldhetnek a mesternek.
			\item D13 - \textit{SCK - Serial Clock}
			A mester által generált óra jel, az adat továbbítás szinkronizációja miatt szükséges.
		\end{itemize}
	\item \textbf{Állapot led}
	Ez egy beépített piros színű miniatűr led, szabadon használható a felhasználó által.
	\item \textbf{Külső megszakítás}
	A D2 és D3 portok INT0 valamint INT1 funkciója biztosítja a külső megszakítást. 
	Erre legtöbbször akkor van szükség amikor valamely kritikus esemény miatt szükséges a mikróvezérlő aktuális feladatát megszakítani, ahhoz hogy figyelmét erre az eseményre fordítsa.
\end{itemize}

Az említett komponenseken kívül a fejlesztő lapon találhatunk még egy B típusú USB portot. 
Ha nem használjuk az USB portot, a táplálást egy külső forrásból is megoldhatjuk a $V_{in}$ és GND portokat használva.
A készülék a 7-12V-os feszültség intervallumban szükséges táplálni.
Továbbá még található egy 5.5V, egy 3.3V-os és még egy GND port amelyek egyéb periferikus áramkörök meghajtására is alkalmasak lehetnek.

\subsubsection{Arduino programozása - Arduino IDE}\subsubsectionro{Programarea Arduino-ului - Arduino IDE }
A fejlesztő lap programozása automatizálva van \cite{ardtut19}. 
A felhasználónak nem szükséges a sokszor körülményes mikróvezérlő felprogramozástól megijednie.
Az Arduino saját fejlesztő környezete az \textbf{Arduino IDE} és a fejlesztőlapra előre megírt boot-loader segítségével ez a folyamat pár egyszerű lépésre redukálódott.
A folyamat a következő egyszerű lépésekre bontható:
\begin{enumerate}
	\item Arduino IDE telepítése a saját számítógépre
	\item Az Arduino driver telepítése az operációs rendszerre
	\item A fejlesztő lap összekötése USB porton keresztül a számítógéppel
	\item Az operációs rendszer port listájában megjelenik egy sajátos azonosítóval a készülék, pl. \textit{COM2}	
	\item A fejlesztő környezet élindítása
	\item A \textit{Tools - Boards} menülistában a fejlesztőlap típusának kiválasztása, pl. \textit{Arduino Nano}
	\item A \textit{Tools - Port} menülistában a helyes port kiválasztása pl. \textit{ez esetben COM2}
	\item A program megírása
	\item A kód kompilálása
	\item A kód feltöltése a fejlesztőlapra
\end{enumerate}

A többi beállításon legtöbbször nem szükséges módosítani.
A fejlesztő környezet igényeli a \textit{C} programozási nyelv ismeretét.
A környezet egy egyszerű két függvényes program implementációt használ:

\begin{lstlisting}[style=CStyle, caption={A \mintinline{cpp}{setup()} és a \mintinline{cpp}{loop()} függvény Arduino IDE-ben },label=fig:arduino_ide_code_eg]
// setup runs once at start or at reset of board
void setup(){
  pinMode(LED_BUILTIN, OUTPUT);
}
// loop repeats itself infintely
void loop() {
  digitalWrite(LED_BUILTIN, HIGH);
  delay(1000);
  digitalWrite(LED_BUILTIN, LOW);
  delay(1000);
}
\end{lstlisting}

A fenti program, a beépített LEDet villogtatja 1 másodpercenként.
A program két jól elkülöníthető részre osztható. 
A \mintinline{cpp}{setup()} függvény a portok és egyéb perifériák iniciálására szolgál. 
Valamint ide írható az összes olyan logika amely induláskor egyszer kell hogy lefusson.
A \mintinline{cpp}{loop()} függvény pedig végtelen ciklus szerűen ismétlődik. 
Az itt található kód összeköthető a belső óra jellel, egy üres \mintinline{cpp}{loop()} függvény például 10 KHz-es frekvenciával fog ismétlődni.
Ez a kód résznek kell tartalmaznia azt a logikát amely megvalósítja a normál működésben elvárt célt.

\subsection{Rádió frekvenciás kommunikáció}\subsectionro{Comunicare pe frecvențe radio}\label{sec:rftcomm}
\subsubsection{NRFL24 rádió frekvencia kommunikációs modul}\subsubsectionro{NRFL24 modul de comunicare pe frecvențe radio}

\begin{wrapfigure}{l}{0.40\textwidth}
	\vspace{-20pt}
    \centering
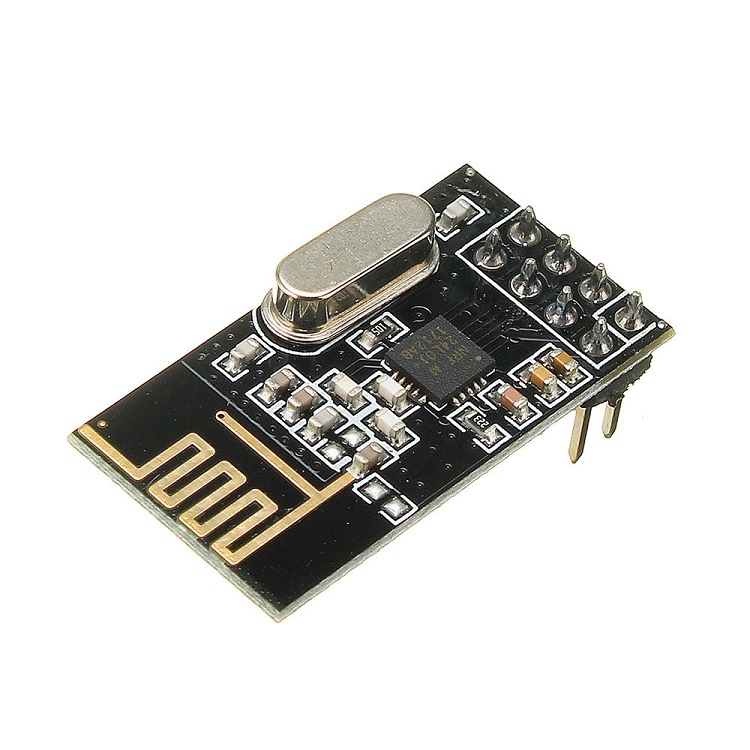
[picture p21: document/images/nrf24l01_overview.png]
    
    \caption[nrf24l01 felülnézet]{nrf24l01 felülnézete}
    \label{fig:nrf24l01overview}
\end{wrapfigure}

Az NRFL24 egy egy csipes rádió adó-vevő készülék. \cite{nosem06}
A világszerte használt 2,4-2,5 GHz-es ISM sávot használja kommunikációs csatornaként.
A főbb képességeit érintve SPI soros kommunikáció segítségével vezérelhető.
1-2 Mbps sebbegésekre képes a levegőn keresztül.
125 rádió frekvenciás csatornán működik.
Nagyon kis mérete és nagyon kis fogyasztása alkalmassá teszi a legtöbb kábel nélküli készülék fejlesztésére.
8 portos kivezetése van amelyek a következőek: 3.3V, GND, CE, CSN, MOSI, SCK, MISO, IRQ.
Amint látható SPI kommunikáció kompatibilis, a már korábban leírt SPI kommunikáció seftiségével könnyen csatlakoztatható az Arduino Nano SPI képes portjaira.
A CE - \textit{Chip Enable} port segítségével aktiváljuk az SPI kommunikációt.
Valamint a CSN - \textit{Chip Select Not} port szerepe hogy életben tartsa ezt.
A 3.3V-os és GND port a táplálásra szolgál. Míg a többi port az SPI kommunikáció alfejezetben leírt feladatokat látja el.

\subsubsection{NRFL24 hálózatok és kommunikációs protokoll}\subsubsectionro{Rețele de NRFL24 și protocol de comunicare}\label{sec:nrlf24rfc}

A \ref{fig:nrf24l01_network}. ábra jelképezi ennek a rádió adó-vevőnek a másik fontos képességét.

\begin{figure}[htp]
	\centering
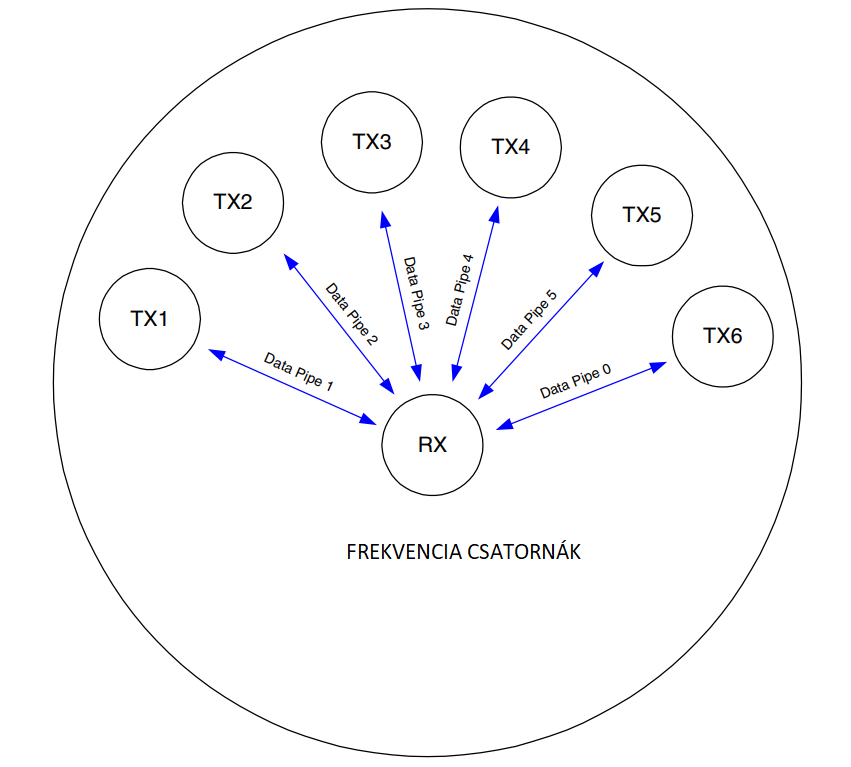
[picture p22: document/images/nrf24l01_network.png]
	
	\caption[nrf24l01 network]{nrf24l01 hálózati kommunikáció mester-szolga módban}
	\label{fig:nrf24l01_network}
\end{figure}

Egyszerű módon lehet ugyan ilyen típusú modulok között kábel nélküli hálózatot kialakítani.
Egy nrf24l01 modul, mester-szolga kapcsolatot létrehozva, egészen 6 darab másik modullal képes digitális adatcsövet fenntartani.
Fontos viszont egyedi címet meghatározni mindegyik modulnak. Hogy a hálózati kommunikáció során tudják azonosítani egymást.
Tovább lépve a fenti példában említett szolgákhoz további 5 modult lehet csatlakoztatni. 
Akik a szolgák szolgái lennének. Ilyen módon 5 szintes mélységig lehet bővíteni a hálózat, elméletileg 3125 modul a fizikai határ.
Ez roppant értékes skálázási szemszögből. Maga a hálózat felépítését bináris fa topológiaként lehet elképzelni.
Adott a mester modul aki az alapot jelképezi, lefele haladva a fán pedig, lehet 5 gyereke, akiknek megint lehet 5 gyereke, stb.

\subsection{74HC595 léptető regiszter}\subsectionro{Registru de deplasare 74HC595}\label{sec:shiftregister}

\begin{wrapfigure}{l}{0.40\textwidth}
	\vspace{-20pt}
    \centering
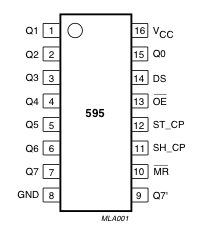
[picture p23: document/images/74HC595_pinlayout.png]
    
    \caption[74HC595 portjai]{74HC595 portjai}
    \label{fig:shiftregister}
\end{wrapfigure}

Sok esetben fordulhat elő, hogy a mikróvezérlőnk digitális kimenetei nem elégségesek az alkalmazásunk összes komponensének a vezérlésére.
Ilyen esetben használunk léptető regisztereket. Egy ilyen alkatrész a 74HC595 léptető regiszter.
Ez egy 8 bites soros-be vagy párhuzamos-ki adatátvitelt biztosít.
Működése a szinkron soros kommunikációra épül.
Röviden mindegyik ciklus órajelre a kívánt adatokat betöltjük bitenként a regiszterbe. 
Miután a teljes byte-nyi adat betöltésre került, a regiszter az egyéni portjain mindegyik biten található \textit{HIGH} vagy \textit{LOW} értéket egyéni portokon továbbítja a vezérelendő komponensekre.
Látható hogy sorosan töltjük be, és párhuzamosan küldjük ki az adatokat. 
Mivel egy óra jelnyi ciklus, nagyon rövid idő (mikró másodpercnyi érték), nem észrevehető az az elvesztett idő amíg 1 Byte betöltődik a regiszterben.
A regiszternek van egy soros kimenet portja is, amely segítségével több regisztert is sorba köthetünk.
Igy egy ciklusban az érkező adat nem csak az aktuális, ha nem a következő regiszter soros bemenetén is megjelenik az adat. Ezt nevezzük léptető regiszterek láncba kötésének.
A \cite{tein19}. forrásban leírt adatlap alapján láthatjuk a \ref{fig:shiftregister}. ábrán a  szilikon csip port elhelyezéseit valamint az \ref{tab:shiftregister}. táblázatban ezek jelentéseit.

\begin{table}[!htbp]
    \centering
    \begin{tabular}{|c|c|} \hline
        Port azonosító & Megnevezés \\ \hline
        $Q_{0} - Q_{7}$ & Párhuzamos kimeneti portok \\ \hline
        GND & Föld  \\ \hline
        $Q_{7'}$ & Soros kimenet \\ \hline
        MR & Mester vissza állítás \\ \hline
        SH\_CP & Regiszter órajel port \\ \hline
        ST\_CP & Regiszter puffer órajel port \\ \hline
        OE & Kimenet aktiválás \\ \hline
        DS & Soros adat bemenetel \\ \hline
        $V_{cc}$ & Táp \\ \hline
    \end{tabular}
    \caption[74HC595 port leírás]{74HC595 léptető regiszter port magyarázat}
    \label{tab:shiftregister}
\end{table}

\subsection{Fotó ellenállás}\subsectionro{Fotorezistoare}

\begin{figure}[htp]
    \centering
    \begin{minipage}{0.45\textwidth}
        \centering
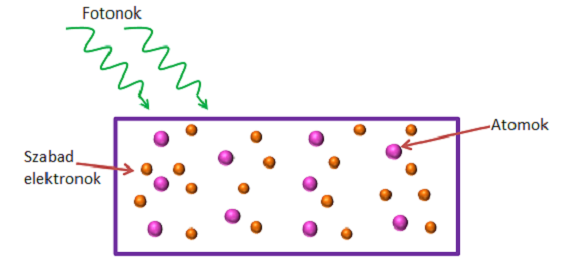
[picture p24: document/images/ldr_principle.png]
        
        \caption[LDR elv]{Fotó ellenállás elvi működés}
		\label{fig:ldr_principle}
    \end{minipage}\hfill
    \begin{minipage}{0.45\textwidth}
        \centering
        
        \caption[LDR struktúra]{Fotó ellenállás felépítése}
		\label{fig:ldr_structure}
    \end{minipage}
\end{figure}

A fotó ellenállás egy egyszerű szenzor. 
Amint a neve is elárulja, lényegében egy olyan elektronikus érzékelő amely fény hatására változtatja ohmikus ellenállását.
Félvezetőként működik, az az külső hatásra, ez esetben fotonok, a CdS (Kadmium szulfit) menetben az atom szintű kötések megbomlanak (\ref{fig:ldr_principle}. ábra).
Ennek következménye képen elektron lyukak és szabad elektronok jelenek meg, és szabad mozgásra képesek az anyagon belül.
A fény hatására a töltés hordozok száma növekszik, tehát az átfolyó áram erőssége is növekszik. 
Áram erősség növekedésének direkt hatása az ellenállás csökkenése. Tehát lényegében a fény erősség növekedése ellenállás csökkenéséhez vezet.
A szakterületen egy gyakori implementációja ennek az elvnek a PGM5516 kóddal ellátott fotó-ellenállás (\ref{fig:ldr_structure}. ábra), amelyet a Token Electronic \cite{toel19} gyártja, és technikai paramétereit a \ref{ldrparams}. táblázatban foglaltuk össze:

\begin{table}[!htbp]
    \centering
    \begin{tabular}{|c|c|c|c|c|c|}\hline
        \specialcell{$V_{max}$\\(VDC)} & 
        \specialcell{$P_{max}$\\(mW)} & 
        \specialcell{Spektrális csúcs\\(nm)} & 
        \specialcell{Ohmikus R\\($k\Omega$)} & 
        \specialcell{Sötétben R\\($M\Omega$)} & 
        \specialcell{Reszponzív idő \\(ms)} \\ \hline
        100 & 90 & 540 &  $2\sim6$ & 0.15  & $30\sim40$  \\ \hline
    \end{tabular}
    \caption[LDR paraméterek]{Fotó ellenállás paraméterei}
    \label{ldrparams}
\end{table}

\subsection{Egyéb szoftverek}\subsectionro{Alte software-uri}
\subsubsection{Fritzing áramkör tervező}\subsubsectionro{Fritzing software de circuit design}
A Fritzing egy nyílt forrás kódú, egyszerűségre törekvő, automatizált áramkör tervező szoftver.
Széles körű adatbázisában a legtöbb elektronikai komponens megtalálható. Továbbá lehetőséget add tesztpanel de nyomtatott áramkör tervezésre is. Mivel egy nyílt forrás kódú termék, a fejlesztése a közösség által történik, és rengeteg anyagot bocsájtanak a felhasználok rendelkezésére \cite{frifo19}.
\subsubsection{Processing UI dizájner}\subsubsectionro{Processing UI designer}
A Processing egy rugalmas, a Java programozási nyelvre alapuló, grafikus interfész vázlatát és kódját implementáló keretrendszer.
Egyszerű megközelítése a kellemes felhasználói felületek készítésére hasonlít az Arduino IDE implementációjára.
Ez is egy függvény orientált környezett, az az a programozó rendelkezésére áll két fő függvény, amelyekben a logika nagy része implementálható.
Természetesen további függvények létrehozhatóak, valamint külső csomagokban osztályok is. Viszont az összes példányosításra, vagy felhívásra, kell hogy kerüljön ebben a két függvényben. 
Ez a két függvény a \mintinline{java}{setup()} és a \mintinline{java}{draw()} függvények. 
Hasonlóan mint az Arduino IDE, itt is az első az inicializálásért, a második pedig a ciklikusan ismétlődő kód futtatásáért fellelős. Mivel egy nyílt forrás kódú termék, a fejlesztése a közösség által történik, és rengeteg anyagot bocsájtanak a felhasználok rendelkezésére \cite{profo19}.

\subsubsection{\LaTeX,  dokumentum szerkesztő}\subsubsectionro{Latex editor de text}
A \LaTeX, egy ingyenes, magas minőségű szöveg szerkesztő és formázó rendszer.
Parancsok által olyan funkciókat tartalmaz, amelyek technikai és tudományos dokumentumok készítésére alkalmas.
A tudományos körökben standard módon elfogadott a publikálandó dokumentumok ebben a rendszerben való készítése.
Mivel egy nyílt forrás kódú termék, a fejlesztése a közösség által történik, és rengeteg anyagot bocsájtanak a felhasználok rendelkezésére \cite{latpro19}.

\newpage
%4
\section{A rendszer célja}\sectionro{Scopul sistemului}
A dolgozat célja egy olyan vasút modell hálózat készítése amely a valóságban található vasút hálózatok működését tükrözi.
Ezt a tanulmányozott ETCS elvek alapján valósítjuk meg, és a következő  alrészekre osztottam, tematika szerint:
\begin{itemize}
	\item \textbf{Mechanikus}: A modell vasút kiegészítő komponensei, amelyek nem a direkt funkcionális működéshez szükségesek. Pl: a vágányokat, jelzőket tartó mechanikus platformok.
	\item \textbf{Hardver}: Azok az elektronikus komponensek összessége, amelyek a mechanikus részre épülve, megvalósítják az architektúra és specifikáció által előírt gépi feladatokat.
	\item \textbf{Szoftver}: Azoknak a programoknak az összessége, amelyek a hardveri komponenseket vezérlik, és elvégzik a rendszer logikai funkcióit.
\end{itemize}

A projekt kivitelezésében alkalmaztam a \ref{cenelecchapter}. fejezetben tanulmányozott V modell (\ref{fig:cenelec_vmodel}. ábra) egyszerűsített változatát. 
Ez alapján történt a követelmények és specifikációk meghatározása, valamint a tényleges megvalósítás is. 
%5
\section{Rendszer követelményei}\sectionro{Cerințele sistemului}
A megvalósítandó rendszer követelményei válaszolnak a \textit{Mit szeretnénk megvalósítani?} kérdésre. A \ref{RAbasics}. fejezetben megismert elvek és a \ref{sec:ptmodell}. fejezetben leírt modell, valamint a korábban említett felosztás alapján a következő táblázatokban (\ref{tab:mechrequirment}, \ref{tab:hardrequirment}, \ref{tab:softrequirment}) szögeztem le mindegyik alrész követelményeit:

\begin{table}[!htbp]
    \centering
    \begin{tabular}{|c|m{12cm}|} \hline
        Nr. & Elvárt mechanikus követelmény\\ \hline
        1 & \specialcell{A vasút vágányokból felépített vágány hálózatnak egy stabil, \\hordozható platform} \\ \hline
        2 & \specialcell{A jelző hálózatot felépítő jelző moduloknak egy mechanikus keret \\ amely biztosítja ezek láthatóságát} \\ \hline
        3 & \specialcell{Az észlelő hálózat, észlelő moduljainak szükséges platform amely \\ az észlelést valamint ennek jelzését megvalósítja} \\ \hline
    \end{tabular}
    \caption[Mechanikai követelmény]{A rendszer mechanikai követelményei}
    \label{tab:mechrequirment}
\end{table}

\begin{table}[!htbp]
    \centering
    \begin{tabular}{|c|m{12cm}|} \hline
        Nr. & Elvárt hardver követelmény\\ \hline
        1 & Mozdony távirányított képességét biztosító hardver \\ \hline
        2 & A mozdony sebességét szabályzó hardver \\ \hline
        3 & A mozdony helyzetét jelző hardver \\ \hline
		4 & Észlelő készülék és hálózat hardver implementáció \\ \hline
		5 & Jelző készülék és hálózat hardver implementáció \\ \hline
		6 & Központi vezérlő rendszer hardver implementáció \\ \hline
		7 & Biztosító rendszer hardver implementáció \\ \hline
		8 & Rendszerek közötti kommunikációt megvalósító hardver\\ \hline
    \end{tabular}
    \caption[Hardver követelmény]{A rendszer hardver követelményei}
    \label{tab:hardrequirment}
\end{table}

\begin{table}[!htbp]
    \centering
    \begin{tabular}{|c|m{12cm}|} \hline
        Nr. & Elvárt szoftver követelmény\\ \hline
        1 & Mozdony vezérlő, hardver szintű, szoftver \\ \hline
        2 & Mozdony vezérlő, számítógépen futó, grafikus interfész \\ \hline
        3 & Észlelő hálózatot, hardver szintű, vezérlő szoftver \\ \hline
		4 & Jelző hálózatot, hardver szintű, vezérlő szoftver \\ \hline
		5 & Központi vezérlő rendszer, hardver szintű, szoftver \\ \hline
		6 & Biztosító rendszert, hardver szintű, vezérlő szoftver  \\ \hline
		7 & Vasút hálózatot követő, számítógépen futó, grafikus interfész \\ \hline
		8 & Rendszer komponensek közötti kommunikációt kezelő szoftver \\ \hline
    \end{tabular}
    \caption[Szoftver követelmény]{A rendszer szoftver követelményei}
    \label{tab:softrequirment}
\end{table}

\newpage
%6
\section{Rendszer architektúra és specifikáció}\sectionro{Arhitectura și specificațiile sistemului}
A követelmények alapján természetes módon körvonalazódik a rendszerünk architektúrája.
A fontosabb komponensek:
\begin{itemize}
	\item Mechanikus komponensek amelyek fizikai alapként szolgálnak a kész hardver rendszernek
	\item A modell mozdony automatizálása különböző hardver és szoftver funkcionalitásokkal
	\item A modell vágány menti észlelő hálózat hardver és szoftver szintű megvalósítása
	\item A modell vágány menti jelző hálózat hardver és szoftver szintű megvalósítása
	\item A rendszerek egységesítse egy központi vezérlő által, valamint a biztosító rendszer fejlesztése
	\item Egy mozdony vezérlő, valamint egy vágány hálózat figyelő grafikus interfész készítése
	\item Az említett hardver és szoftver komponensek közötti kommunikáció megoldása
\end{itemize}

\begin{figure}[htp]
	\centering
	
	\caption[Rendszer tömbvázlat]{A modell vasút rendszer tömbvázlata }
	\label{fig:block_diagram_sysra}
\end{figure}

A tömbvázlatban használt rövidítések magyarázata a \ref{tab:specabrv}. táblázatban található.
\begin{table}[htp]
    \centering
    \begin{tabular}{|c|l|l|l|} \hline
        Nr. & Rövidítés & Angolul & Magyarázat \\ \hline
		1 & DB-MC & Dev. Board with MCU & Fejlesztőlap Mikróvezérlővel \\ \hline
		2 & RFT & Radio Frequency Transreciever & Rádió frekvenciás adó-vevő \\ \hline
		3 & LDR & Light Dependent Resistor & Fotó ellenállás \\ \hline
		4 & TM & Train Module & Mozdony modul \\ \hline
		5 & VM & Vacancy Module & Észlelő modul \\ \hline
		6 & SM & Signal Module & Jelző modul \\ \hline
		7 & ACC & Areal Central Controller & Területi központi vezérlő \\ \hline
		8 & IL & InterLocking & Óvó/Biztosító rendszer \\ \hline
		9 & TC-GUI & Train Control - GUI & Mozdony vezérlő g.i. \\ \hline
		10 & RN-GUI & Rail Network - GUI & Vágány hálózat állapot g.i. \\ \hline
		11 & PSU & Power Supply Unit & Áramszolgáltató egység \\ \hline
		12 & USB-USB B & USB to USB B channel & UI és CCM közötti soros kom. \\ \hline
		13 & SPI & Serial Peripheral Interface & Soros periféria interfész \\ \hline
		14 & RFC & Radio Frequency Channel & Rádió Frekvenciás Kanális \\ \hline
		15 & SR & Shift Register & Léptető regiszter \\ \hline
		16 & DCM+C & DC Motor + Controll & DC Motor + vezérlés \\ \hline
		17 & TIP & Train Integrity Position & Vonat teljesség helyzete \\ \hline
	\end{tabular}
    \caption[Rövidítések]{Használt rövidítések magyarázata}
    \label{tab:specabrv}
\end{table}

A \ref{RAbasics}. fejezet alapján meghatározható hogy a modell vasút hálózatra a következő ETCS ás vasúti elvek alkalmazhatóak:
\begin{itemize}
	\item ETCS 2-es szintű ATP rendszer 
	\item Zárt hálózat amely exkluzív fővágányokból épül fel
	\item A műanyagból gyártót vágányok kizárják a pályaáramkör használatát, tehát valamilyen tengelyszámláló megoldás szükséges
	\item A standard jelző aspektusok használata (\textit{piros - sárga - zöld})
	\item Óvó - Biztosító rendszer implementációja
	\item Automatikus blokk elv implementációja egy 8 blokkból álló kör szekvenciás rendszerre
\end{itemize}

Ezt leszögezve és kibővítve, a követelményekkel valamint a \ref{theory_section}. fejezetben tanulmányozott hardver és szoftver megoldássokkal a \ref{fig:block_diagram_sysra}. ábrán látható tömbvázlatot készítettem.
Továbbiakban mindegyik komponens specifikációját vázoljuk fel, a követelmények alapján.

\subsection{Mechanikus specifikációk}\subsectionro{Specificațiile mecanice}\label{sec:mechspec}
A \textbf{Pequtren} módell vasút méreteit ismerve ($L = 2,94 m$), a kör alakú zárt vágány pálya $D = 1 m$ átmérővel rendelkezik.
Ennek egy  $105 \times 105 cm$ pár milliméter vastagságú lemez alkalmas.

A jelző készüléknek szükséges egy kis felület ahova a "jelző lámpákat" rögzíthetjük, valamint a teljes készüléket, egy csavaros megoldással, a hálózat platformhoz rögzíthetjük.

Az észlelő készüléknek is egy kis felületre kell rögzítettünk az észlelő szenzort és az állapot jelző LEDet. Végül ez is egy csavaros megoldással rögzítődik a platformhoz. 

Ezeknek a mennyiségét, az architektúrában meghatározott blokkok mennyisége határozza meg, tehát 8 jelző és észlelő készülék legyártása szükséges.

\subsection{Hardver specifikációk}\subsectionro{Specificațiile hardwareului}
A hardver specifikációkat a \ref{tab:hardrequirment}. táblázatban leszögezett követelmények alapján a \ref{tab:hardspec} táblázatban foglaltam össze, használva a \ref{tab:specabrv} táblázatban definiált rövidítéseket:

\begin{table}[!htbp]
    \centering
    \begin{tabular}{|c|c|l|} \hline
        Nr. & Köv. & Megfelelő hardver specifikáció \\ \hline
        1 & 8.1 & \specialcell{A TM távirányítása ACC végzi el DB-MC, RFT+RFC és PSU (9V) 
                            \\komponensekkel valósul meg} \\ \hline
        2 & 8.2 & \specialcell{A TM sebesség szabályozását a DM-MC és egy kibővítő DCM+C, 
                            \\PSU (3V) áramkör valósítja meg}  \\ \hline
        3 & 8.3 & \specialcell{A TM a TIP funkciót fény forrás rögzítése oldja
                            \\meg, DB-MC irányítja} \\ \hline
		4 & 8.4 & \specialcell{Az VM egy LDR megoldást alkalmaz, érzékelve a 3-as specifikációban
		                    \\TIP jelet. Az automata blokkok meghatározása szerint, mind a 
		                    \\8 blokkban szükséges egy LDR áramkör. Az LDR adatok a DB-MC 
		                    \\analóg bemeneteire kapcsolódnak. Az DB-MC, PSU(9V) táplálja,
		                    \\és RFT-en keresztül továbbítja az adatokat ACC felé}\\ \hline
		5 & 8.5 & \specialcell{Az SM-t, az ACC vezéreli DB-MC, RFT + RFC és PSU (9V) 
		                    \\segítségével SM a VM által szolgáltatott adatok alapján
		                    \\számolja a szükséges jelzést. Mivel DB-MC digitális 
		                    \\kimenetei korlátozottak 3 SR állítja be a jelzést}\\ \hline
		6 & 8.6 & \specialcell{ACC RFT és RFC-n keresztül irányítja a rendszer logikát ACC 
		                    \\USB B - USB soros kapcsolatban van TC-GUI és RN-GUI-l}\\ \hline
		7 & 8.7 & \specialcell{IL az ACC szinten valósul meg, valójában hardver szintű szoftver} \\ \hline
		8 & 8.8 &\specialcell{Modulok közötti kommunikációt az RFT hálózat RFC-n keresztül 
		                    \\valósítja meg}\\ \hline
    \end{tabular}
    \caption[Hardver specifikáció]{A rendszer hardver specifikációi}
    \label{tab:hardspec}
\end{table}

\subsection{Szoftver specifikációk}\subsectionro{Specificațiile software-ului}
A szoftver specifikációkat a \ref{tab:softrequirment}. táblázatban leszögezett követelmények alapján a \ref{tab:softspec}. táblázatban foglaltam össze, használva a \ref{tab:specabrv}. táblázatban definiált rövidítéseket:

\begin{table}[!htbp]
    \resizebox{\textwidth}{!}{
    \begin{tabular}{|c|c|l|} \hline
        Nr. & Köv. & Megfelelő szoftver specifikáció \\ \hline
        1 & 9.1 & \specialcell{A TM távirányítását DB-MC-n futó szoftver hajtja végre. A végrehajtó
                            \\parancsok ACC-tol érkeznek RFC protokollal az RFT hálózaton keresztül.
							\\TM értelmezi az RFC protokollt. A TIP jelzés szoftverből 
							\\bekapcsolható. A sebesség szabályozás PWM modulációval programozható.
							\\TM továbbítja ACC-nek a sebesség aspektusát is. TM az ACC-tól érkező
							\\megállj parancsot azonnal elvégzi.} \\ \hline
        2 & 9.2 & \specialcell{A TC-GUI a parancsok elsődleges forrása. Két sebesség szint és egy 
                            \\ megállás parancsot kezdeményez. Opcionálisan jelezheti a következő
							\\ SM aspektust is.}  \\ \hline
        3 & 9.3 & \specialcell{A VM a begyűjtött LDR adatokat csomagban rendezi. A VM folytonosan 
                            \\továbbítja az aktuális csomagot ACC-nek. RFC protokollal az RFT hálózaton
							\\keresztül. A VM érzékelt bemenet esetén egy állapot jelzést aktivál.} \\ \hline
		4 & 9.4 & \specialcell{Az SM ACC-tól, RFT hálózaton érkező csomagot feldolgozza. SM is tudja  
		                    \\értelmezni az RFC protokollt. SM a megfelelő SR-ek aktiválásával vezérli 
		                    \\a jelzőket. SM folyamatosan várja az ACC-től érkező jeleket.}\\ \hline
		5 & 9.5 & \specialcell{ACC felügyelő, továbbító, vezérlő és értelmező szerepe van. ACC 
		                    \\kapcsolatban van UI komponensekkel, fogadja az innen érkező parancsokat.
							\\ACC az RFT hálózat központi komponense, RFC képes. Fogadja a VM-l
							\\értekező csomagokat. Átadja IL-nek. Fogadja a TM-töl érkező csomagot,
							\\ Átadja IL-nek. Átveszi IL-l érkező csomagot, továbbítja TM és SM-nek.}\\ \hline
		6 & 9.6 & \specialcell{IL az ACC-ben kódolt biztosító függvények összessége. IL értelmezi az 
		                    \\előkészített VM csomagot. IL értelmezi a fogadott TM információt.
							\\IL 4 blokkos jelző aspektus szekvencia algoritmust futtat. Az algoritmus
							\\kiszámolja a szükséges biztonságos aspektust a hálózat összes SM 
							\\komponensének. IL átadja a számolt eredményt ACC-nek. IL automatikusan
							\\értesíti ACC-t ha TM sebesség aspektusa nem felel meg a jelző aspektusnak.}\\ \hline
		7 & 9.7 & \specialcell{Az IL-től érkezett aspektus csomagot ACC RN-GUI-nak is továbbítja. 
							\\Valamint a figyelmeztető parancsot sebesség határ túllépése esetén 
							\\továbbítja TC-GUI-nak is.} \\ \hline
		8 & 9.8 &\specialcell{ACC és UI komponensek standard soros porton kommunikálnak. ACC,  
		                    \\VM, TM, SM egymás között, szoftverből irányítottan, az RFT 
							\\hálózaton, a fejlesztendő RFC protokollal kommunikálnak.}\\ \hline
    \end{tabular}
    }
    \caption[Szoftver specifikáció]{A rendszer szoftver specifikációi}
    \label{tab:softspec}
\end{table}

\newpage
%7
\section{Részletes tervezés és megvalósítás}\sectionro{Planificare detaliată și realizarea}
A dolgozat megvalósítása a \ref{fig:block_diagram_sysra}. ábrán bemutatott architektúra tömbvázlata, és a követelmények valamint specifikációk alapján mechanikai, hardver és szoftver alrészekre osztható.
A specifikációkban meghatározott rövidítéseket az egyszerűség kedvéért továbbra is használjuk. 
A specifikációt követve mindegyik komponens megvalósítását külön alfejezetben részletezzük.

\subsection{Mechanikai kivitelezés}\subsectionro{Implementare mecanică}
\subsubsection{Vágány hálózat platform}\subsubsectionro{Platforma pentru rețeaua de șine}
A \ref{sec:mechspec}. fejezet szerinti specifikáció alapján az első lépésben egy MDF (Medium Density fibreboard) lapot terveztem a platform elkészítéséhez.
Viszont kimérve a $1050\times1050mm$ méretű lapot, a súlya túl nagynak bizonyult. 
És mivel szempont a platform relatív mobilitása, végül egy natúr $3mm$-es vastagságú HDF-lapot választottam, amelyet erre a méretre vágtam ki.
Viszont ebben a méretben a HDF lap már túl hajlékony, éppen ezért szükségesnek tartottam egy támasztó rács szerkezetet építeni a HDF-lapra.
Ezt $1000\times20mm$-es farudakkal valósítottam meg (\ref{fig:railnetworkplatfromback}. ábra).
A kész platformra fekete nejlon kábelszorítóval több pontban rögzítettem a műanyag vágányokat (\ref{fig:railnetworkplatformfront}. ábra).
\begin{figure}[htp]
    \centering
    \begin{minipage}{0.45\textwidth}
        \centering
        
        \caption[Hálózat platform felül]{Hálózat platform felülnézete}
		\label{fig:railnetworkplatformfront}
    \end{minipage}\hfill
    \begin{minipage}{0.45\textwidth}
        \centering
        
        \caption[Hálózat platform alul]{Hálózat platform alulnézete}
		\label{fig:railnetworkplatfromback}
    \end{minipage}
\end{figure}

\subsubsection{Jelző és észlelő platform}\subsubsectionro{Platforma pentru semnalizare și detectare}
A \ref{sec:mechspec}. fejezet szerinti specifikáció szerint, a 8 blokk méretű hálózatunknak, 8 darab jelző és észlelő platform szükséges.
A platformokat fekete $3mm$ vastagságú plexid lemezből készítettem, mivel tetszetős a színe és könnyen megmunkálható az anyag.
A jelző platformnak a három szín aspektus mellet, két rögzítési pontot is biztosítottam.
A rögzítést $4mm$-es hexagonális csavarokkal (apa, anya és dísz) oldottam meg.
A szín aspektusokat jelző LED-eknek tehát $3x7mm$-es, a rögzítésnek pedig $2x4mm$-es lyukakat készítettem a $40\times40mm$ méretűre tervezett lapra (\ref{fig:signalplatform}. ábra).
Az észlelőnek pedig $2x7mm$-es, az állapot LED-nek és szenzornak, és egy $4mm$-es, a rögzítésnek, lyukat fúrtam. Mérete pedig $20\times40mm$ (\ref{fig:vacancyplatform}. ábra).
Az alkatrész tartó lyukakban $7mm$ átmerőjű LED foglalatokat helyeztem.

\begin{figure}[htp]
    \centering
    \begin{minipage}{0.45\textwidth}
        \centering
        
        \caption[Jelző platform]{Elkészített jelző platform}
		\label{fig:signalplatform}
    \end{minipage}\hfill
    \begin{minipage}{0.45\textwidth}
        \centering
        
        \caption[Észlelő platform]{Elkészített észlelő platform}
		\label{fig:vacancyplatform}
    \end{minipage}
\end{figure}

\subsection{Hardver kivitelezés}\subsectionro{Implementarea hardware-ului}
A rendszer hardver lelke az \textbf{Arduino Nano} fejlesztőlap. Ezt a fejlesztő lapot több okból kifolyólag választottam.
Első sorban egyszerűen és gyorsan felprogramozható, amint a \ref{sec:arduinonano}. fejezetben megbizonyosodhatunk róla.
Továbbá nagyon jó teljesítmény/költség aránnyal rendelkezik, a dolgozat írásának időpontjában 10-15 RON körül lehet beszerezni.
Végső sorban pedig kis fizikai méretezésnek köszönhetően, több rendszerben is egyszerűen integrálható. Éppen ezért mindegyik modul TM, SM, VM és ACC tartalmaz egy ilyen lapot a modul sajátos hardver vezérlése végett.
Valamint az információ továbbítás miatt, mindegyiket kibővítettem egy RFC kommunikációra képes RFT képes áramkörrel.
Ez a mi esetünkben a \ref{sec:rftcomm} fejezetben bemutatott \textbf{NRFL24} rádió frekvencia kommunikációs modul.
\subsubsection{Modulok közötti kommunikáció}\subsubsectionro{Comunicare între moduluri}\label{sec:RFTandRFC}
A \ref{sec:rftcomm} fejezetben leírt adatok alapján hardver szinten csak a \ref{tab:nrf24l01ports}. táblázathoz csatolt áramkört szükséges megvalósítani.
Az NRF24L01 által képviselt RFT-t SPT kommunikáció seftiségével vezérli a DB-MC.
Ezt a \ref{tab:nrf24l01ports} táblázatbeli port párosítás szerint végezzük el.

\begin{table}[htp]
	\begin{minipage}{0.5\linewidth}
		\centering
		\begin{tabular}{|c|c|}\hline
			DB-MC port & Megfelelő RFT port \\ \hline
			GND & GND \\ \hline
			3V3 OUT & $V_{cc}$ \\ \hline
			D9 & CE \\ \hline
			D10 & D10 \\ \hline
			D13/SCK& SCK \\ \hline
			D12/MISO & MOSI \\ \hline
			D11/MOSI & MISO \\ \hline
		\end{tabular}
	\end{minipage}\hfill
	\begin{minipage}{0.45\linewidth}
		\centering
		
	\end{minipage}
	\caption[NRF24L01 bekötése]{NRF24L01 portjainak bekötése DB-MC-ben}
	\label{tab:nrf24l01ports}
\end{table}
Ezen túl hardver szinten nincs több feladatunk az RFT-vel kapcsolatosan, a rádiófrekvenciás hálózat és kommunikáció szoftver szintű vezérléssel valósul meg.

\subsubsection{Mozdony modúl}\subsubsectionro{Modulul de locomotivă}
A modell mozdony egy egyszerű, gyárilag, készen előállított, egyen árammal működő mozgó jármű. Tartalmaz egy egyenáramú motort, melyet egy 3 voltos elem telep hajt meg.
Valamint egy kapcsoló található rajta amit bekapcsolva, a mozdony azonnal mozgásba kerül.
Ez jelenti a kiindulási pontot. Célunk része ezt az egyszerű járművet digitalizálni, több funkcionalitás végrehajtására is képessé tenni, felhasználva a \textit{\nameref{theory_section}} fejezetben tanultakat.
A dolgozat keretein belül \ref{tab:hardspec}. táblázatban 1,2 és 3-as sorában leírt specifikációkkal bővítve a mozdonyt véglegesítjük a TM hardvert:
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

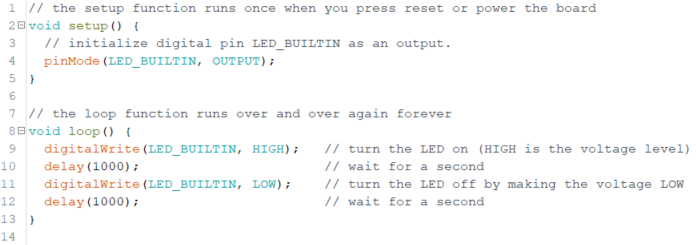
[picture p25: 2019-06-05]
document/images/adruino_ide_code_eg.png

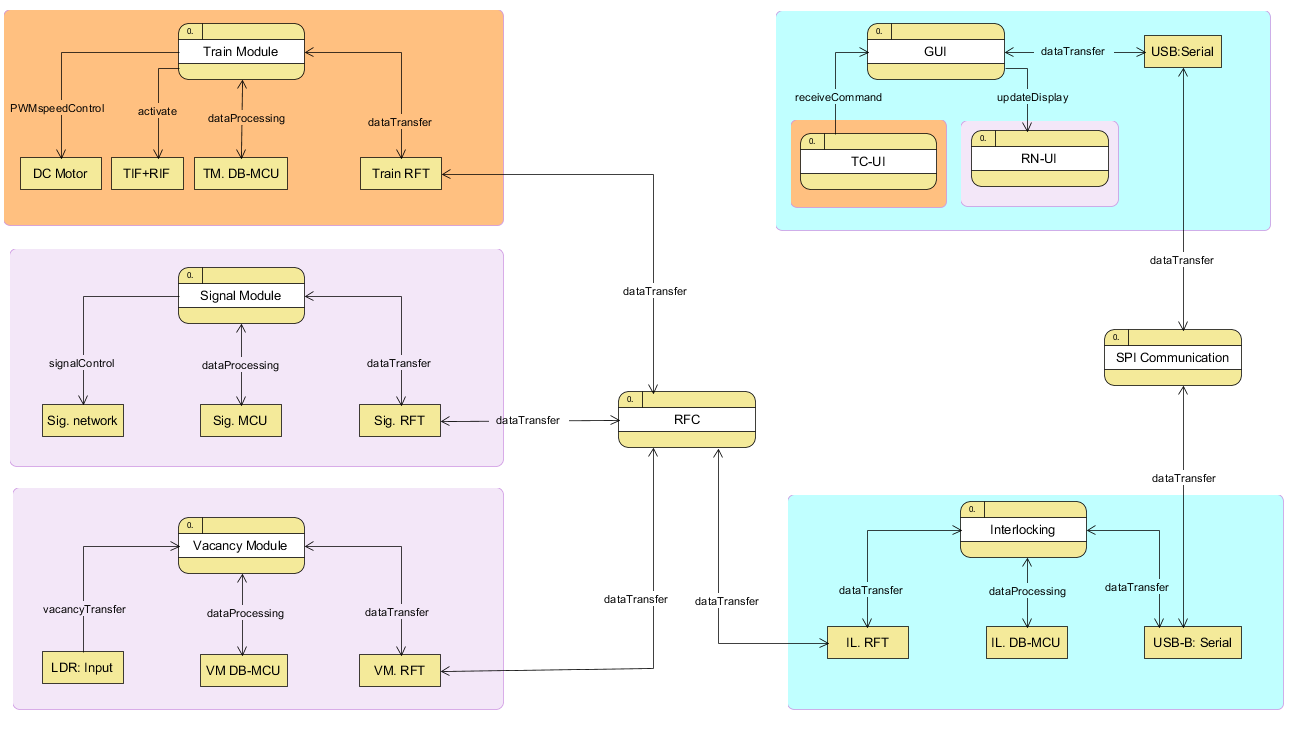
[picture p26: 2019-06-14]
document/images/ra_data_flow_diagram.png

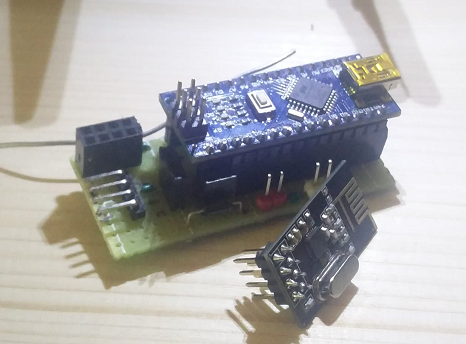
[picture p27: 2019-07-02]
document/images/TMboard.png

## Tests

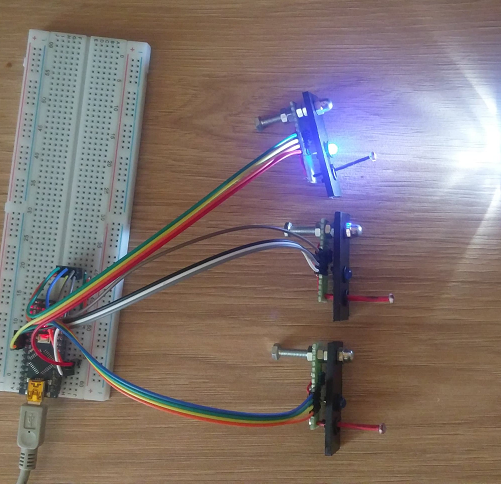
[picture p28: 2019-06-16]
document/images/vm_test_2.png

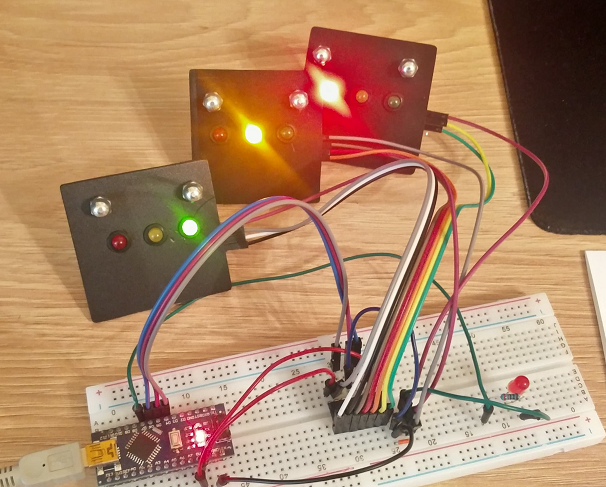
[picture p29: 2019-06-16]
document/images/sm_test_3.png

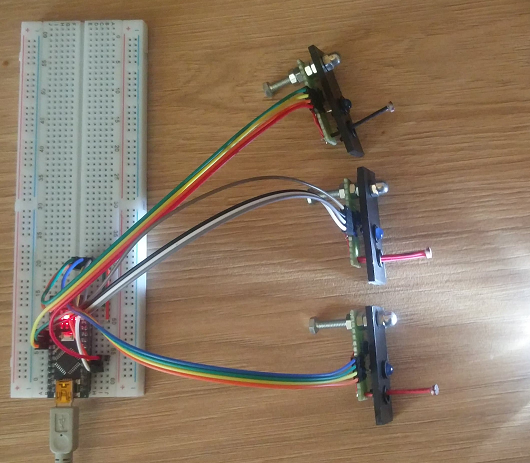
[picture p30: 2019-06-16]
document/images/vm_test_1.png

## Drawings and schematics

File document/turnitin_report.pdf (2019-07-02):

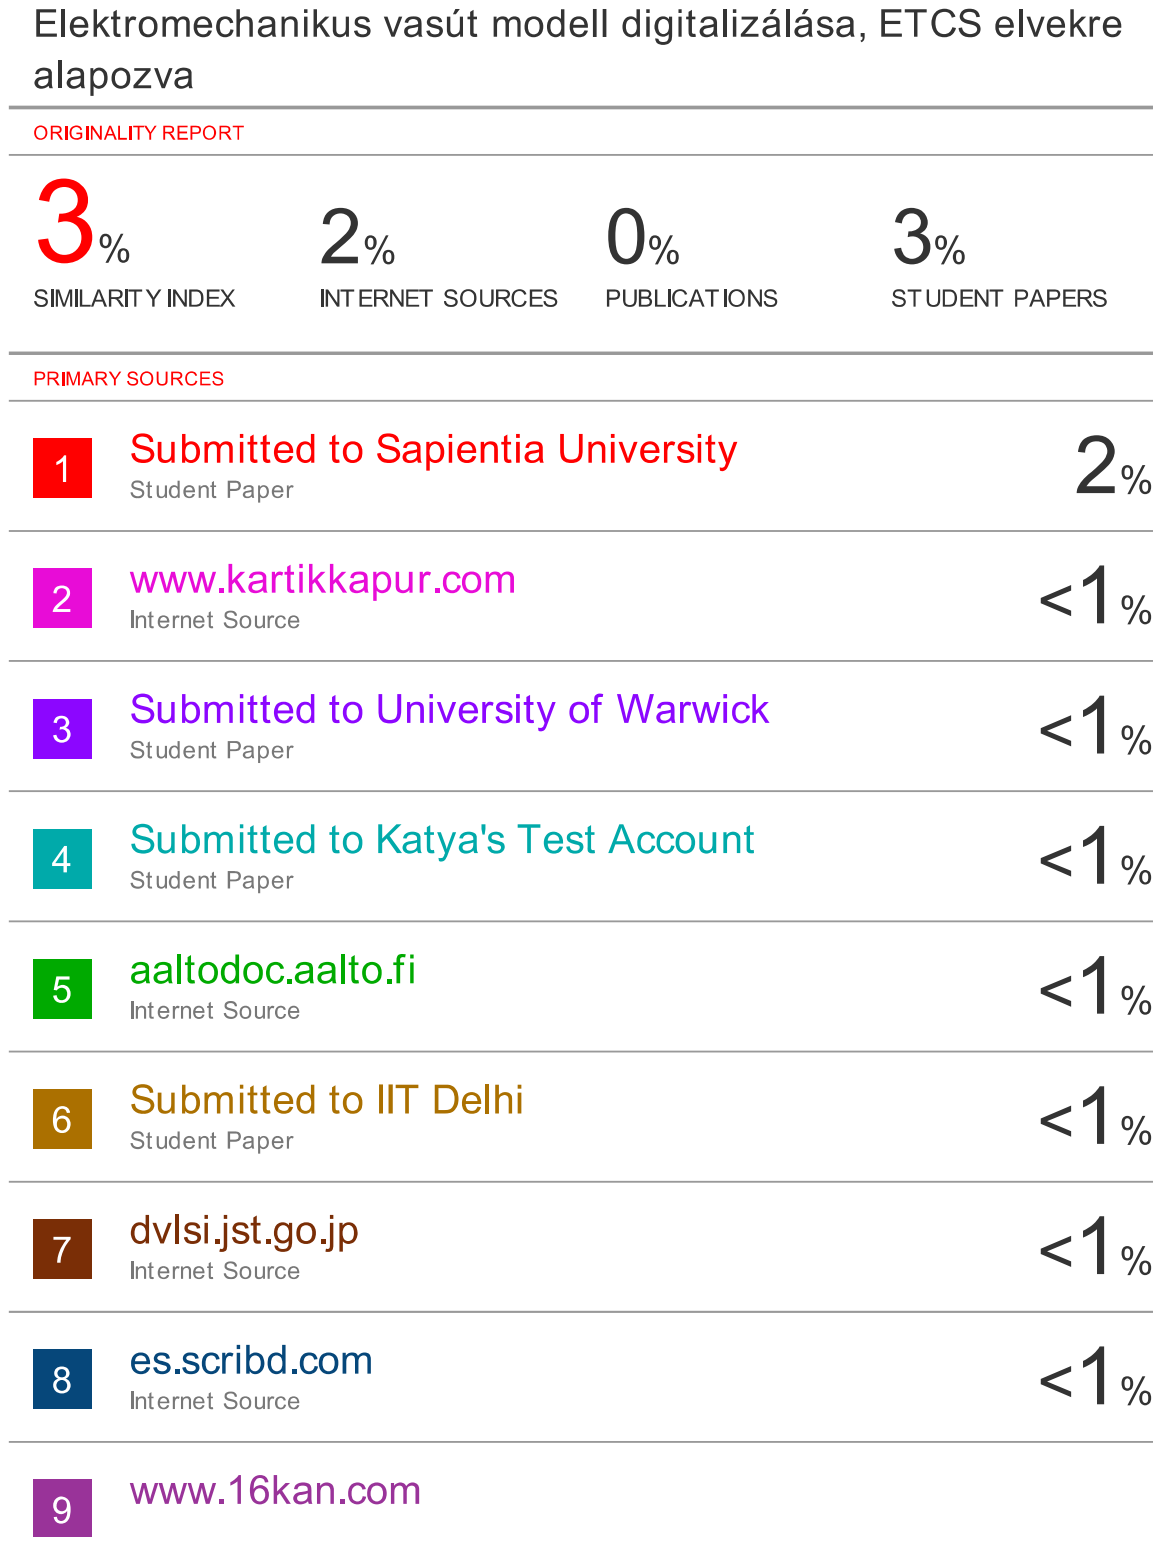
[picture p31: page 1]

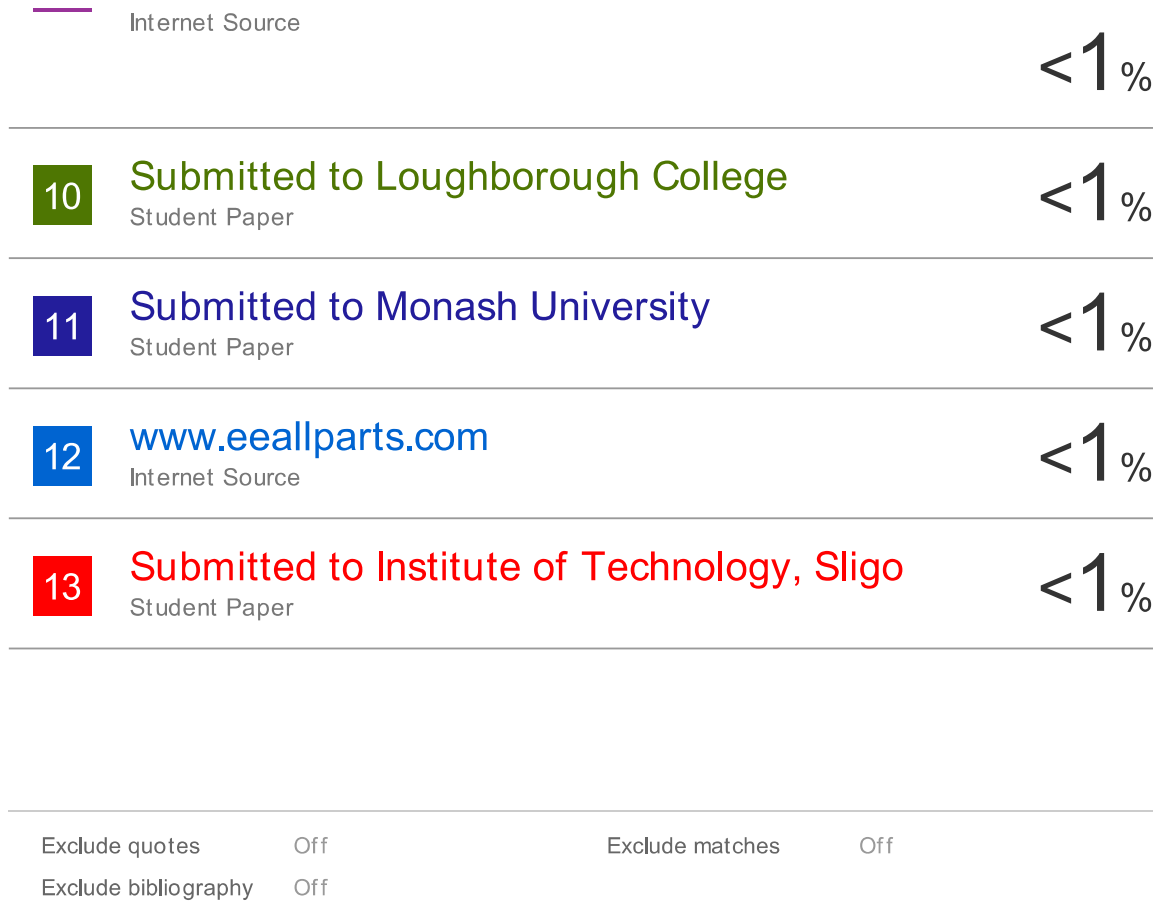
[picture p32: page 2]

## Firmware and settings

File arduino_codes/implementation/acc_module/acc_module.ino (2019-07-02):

/*
    Railway hardware Areal Computer Control module
          == Master Node at adress 00 ==
                  by Gábor Zsolt
*/

/* include libraries for NRF24L01
    SPI.h for SPI communication via MOSI,MISO, SCK pins
    RF24.h for for controlling individual NRF24L01 modules via the CSN and CE pins
    RF24Network.h for the NRF24L01 module network
*/

#include <RF24Network.h>
#include <RF24.h>
#include <SPI.h>

// initialize buffer values
const int data_size = 8;
const int train_num = 2;
char ui_package[2 * data_size];

// initialize radio network values
RF24 radio(9, 10);                  // NRF24L01 (CE,CSN)
RF24Network network(radio);         // include this module in the network
const uint16_t node_acc = 00;      // master node adress
const uint16_t node_vacancy = 01;     // vacancy control module adress
const uint16_t node_signal = 02;    // signal netwrok control adress
const uint16_t node_train_1 = 03;   // train network control adress
const uint16_t node_train_2 = 04;
int fromUI = 0;
const byte numChars = 3;
boolean newData = false;
String speed_serial = "";

/*  Signal data initialization
    The message contains infromation about the 8 signals and their aspectsa
    The 8 characters between represent in units of one a signal and a letter representing the signals aspect
 	The numeric identifier of a specific signal is represented by the index of the array
    Possible aspects: R - RED (also default value)
                      Y - YELLOW
                      G - GREEN
    Number of signals go from 1 to 8.
    Example: RRYGRYGR
              signal 1 has aspect RED
              signal 2 has aspect RED
              signal 3 has aspect YELLOW
              signal 4 has aspect GREEN
              signal 5 has aspect RED
              signal 6 has aspect YELLOW
              signal 7 has aspect GREEN
              signal 8 has aspect RED
*/
char central_signal[data_size] = "RRRRRRRR";

/*  Vacancy data initialization
    The message contains infromation about the 8 vacancy elements and their state
    The 8 characters represent in units of one a track/block and a letter representing the state
 	The numeric identifier of a specific block is represented by the index of the array
    Possible states: F - FREE (also default value)
                     O - OCCUPIED
    Number of blocks go from 1 to 8.
    Example: FFOFFOFF
              block 1 is FREE
              block 2 is FREE
              block 3 is OCCUPIED
              block 4 is FREE
              block 5 is FREE
              block 6 is OCCUPIED
              block 7 is FREE
              block 8 is FREE
*/
char central_vacancy[data_size] = "FFFFFFFF";

/* Train data initialization
   The messeage contains data about the trains present in the network and their speed aspect
   The character represents the train state and speed
   Based on layout design at most 2 trains can be present in the rail network at a time
   Possible states:  N - NOT (also default, means train is not on track)
                     S - STOP (train on track and stopped)
                     H - HALF (train on track and moves with half speed)
                     M - MAX (train on track and moves with max speed)
*/

char central_train[train_num] = "NN";

//setup run at startup once
void setup() {
  //initialize radio frequency network to communicate between modules
  SPI.begin();
  radio.begin();
  network.begin(90, node_acc);
  //setup Serial Port communication with UI on the control PC, once in loop it is guaranteed that Serial connection is set up, this way no connection is done
  Serial.begin(19200);
  establishContact();
}

void loop() {
  // connect to RTF network
  network.update();
  //receive data from network
  while (network.available()) {
    RF24NetworkHeader master_header;
    char receivedData[data_size];
    network.read( master_header, &receivedData, sizeof(receivedData));

    //receiving and load into local buffer information from vacancy module
    if (master_header.from_node == node_vacancy) {
      for (int i = 0; i < sizeof(receivedData); i++)
        central_vacancy[i] = receivedData[i];
    }
  }
  //calculate signal aspect sequencing
  interlocking();

  //Read from Serial port incomming train speed from TN-UI and send update to ui
  recvSerial();
  // send new speed data via RFC to SM
  send_signal_data();
  // send new aspect data via RFC to TM
  send_train_data();
  //wait a litle so all data has time to arrive
  delay(10);
  
}

void establishContact() {
  while (Serial.available() <= 0) {
    Serial.print('A');   // send a capital A
    delay(300);
  }
}


void recvSerial() {
  if (Serial.available() > 0) {
    fromUI = Serial.read();
    //handle cases for fromUI
    convert_speed_to_char(fromUI);
    for (int i = 0; i < data_size; i++)
      Serial.write(central_vacancy[i]);
    for (int i = 0; i < data_size; i++)
      Serial.write(central_signal[i]);
  }
}

void convert_speed_to_char(char data) {
  switch (data) {
    case 'B':
      central_train[0] = 'S';
      central_train[1] = 'S';

      break;
    case 'C':
      central_train[0] = 'S';
      central_train[1] = 'H';
      break;
    case 'D':
      central_train[0] = 'S';
      central_train[1] = 'M';
      break;
    case 'E':
      central_train[0] = 'H';
      central_train[1] = 'S';
      break;
    case 'F':
      central_train[0] = 'H';
      central_train[1] = 'H';
      break;
    case 'G':
      central_train[0] = 'H';
      central_train[1] = 'M';
      break;
    case 'H':
      central_train[0] = 'M';
      central_train[1] = 'S';
      break;
    case 'I':
      central_train[0] = 'M';
      central_train[1] = 'H';
      break;
    case 'J':
      central_train[0] = 'M';
      central_train[1] = 'M';
      break;
    default:
      central_train[0] = 'S';
      central_train[1] = 'S';
      break;
  }
}

//interlocking caluclations based on received data
void interlocking() {
  //verify number of trains in network
  int train_num =  count_train();
  //run SIAS algorithm
  sias(train_num);
}

// Signal Aspect Sequencing Algorithm
void sias(int t) {
  //overwrite previous aspects, in each new calculation the old aspects must be disregarded, as a security feature, the algorithm makes calculations on actual data
  for ( int i = 0; i < data_size; i++) {
    central_signal[i] = 'D';
  }
  // value to hold overflow of circular buffer boundry
  int end_ar = 0;
  //loop through vacancy array and set signal aspects according to Occupied blocks
  for ( int i = 0; i < data_size; i++) {
    // since division is used on the iterator, handle case of negative value
    if ( i - 1 < 0)
      end_ar = (i - 1) % data_size + data_size;
    //no conflict case, plenty of distance between blocks
    if (  (central_vacancy[i % data_size] == 'O' && central_vacancy[(i + 1) % data_size] == 'F' && central_vacancy[(i + 2) % data_size] == 'F' && central_vacancy[(i + 3) % data_size] == 'O'  ) ||
          (central_vacancy[i % data_size] == 'O' && central_vacancy[(i + 1) % data_size] == 'F' && central_vacancy[(i + 2) % data_size] == 'F' && central_vacancy[(i + 3) % data_size] == 'F' && central_vacancy[(i + 4) % data_size] == 'O')) {
      central_signal[i % data_size] = 'R';
      central_signal[(i + 1) % data_size] = 'G';
      if ( i - 1 < 0) {
        central_signal[end_ar] = 'Y';
      } else {
        central_signal[(i - 1) % data_size] = 'Y';
      }
      //cout<<"OFFO OFFFO"<<"\n";
      //issue SPEED_MAX command
    }
    // OFO conflict, since upcomming Red or Yellow aspect can not be overwritten
    if (central_vacancy[i % data_size] == 'O' && central_vacancy[(i + 1) % data_size] == 'F' && central_vacancy[(i + 2) % data_size] == 'O' ) {
      central_signal[i % data_size] = 'R';
      central_signal[(i + 1) % data_size] = 'Y';
      central_signal[(i + 2) % data_size] = 'R';
      central_signal[(i + 3) % data_size] = 'G';
      if ( i - 1 < 0) {
        central_signal[end_ar] = 'Y';
      } else {
        central_signal[(i - 1) % data_size] = 'Y';
      }
      //issue SPEED_MIN command
      //cout<<"OFO"<<"\n";
    }
    // OO conflict, adjacent blocks are occupied, the train downstream can't overwrite upstream Red aspect
    if (central_vacancy[i % data_size] == 'O' && central_vacancy[(i + 1) % data_size] == 'O' ) {
      central_signal[i % data_size] = 'R';
      central_signal[(i + 1) % data_size] = 'R';
      central_signal[(i + 2) % data_size] = 'G';
      if ( i - 1 < 0) {
        central_signal[end_ar] = 'Y';
      } else {
        central_signal[(i - 1) % data_size] = 'Y';
      }
      //issue STOP command
      //cout<<"OO"<<"\n";
    }
    // simple case of one train, and case of 4 block distance between two trains
    if ((t == 1 && central_vacancy[i % data_size] == 'O') ||
        (central_vacancy[i % data_size] == 'O' && central_vacancy[(i + 1) % data_size] == 'F' && central_vacancy[(i + 2) % data_size] == 'F' && central_vacancy[(i + 3) % data_size] == 'F' && central_vacancy[(i + 4) % data_size] == 'F' && central_vacancy[(i + 5) % data_size] == 'O')) {
      central_signal[i % data_size] = 'R';
      central_signal[(i + 1) % data_size] = 'G';
      if ( i - 1 < 0) {
        central_signal[end_ar] = 'Y';
      } else {
        central_signal[(i - 1) % data_size] = 'Y';
      }
      // issue SPEED_MAX command
    }
  }
  // since D-default value is not a valid aspect, replace the new signal aspect array D values with Red aspect
  for (int i = 0; i < data_size; i++) {
    if (central_signal[i] == 'D')
      central_signal[i] = 'R';
  }
}

//central_train buffer can be inaccurate, field sensor input is considered more valid, so based on it we calculate the number of trains in the network
int count_train() {
  int val = 0;
  for ( int i = 0; i < data_size; i++) {
    if (central_vacancy[i] == 'O')
      val++;
  }
  return val;
}

//send updated signal data to signal network hardware
void send_signal_data() {
  RF24NetworkHeader header_to_sig(node_signal);
  bool ok_sig = network.write(header_to_sig, &central_signal, sizeof(central_signal));
}

//send received data from UI to control train module
void send_train_data() {
  char speed_t1 = central_train[0];

  RF24NetworkHeader headert1(node_train_1);
  bool ok_t1 = network.write(headert1, &speed_t1, sizeof(speed_t1));
  }

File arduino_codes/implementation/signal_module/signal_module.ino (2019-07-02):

/*
          Railway hardware Signal module
          == Slave Node at adress 02 ==
                  by Gábor Zsolt
*/

/* include libraries for NRF24L01
    SPI.h for SPI communication via MOSI,MISO, SCK pins
    RF24.h for for controlling individual NRF24L01 modules via the CSN and CE pins
    RF24Network.h for the NRF24L01 module network
*/

//Headers for Radio network
#include <RF24Network.h>
#include <RF24.h>
#include <SPI.h>

//Pin declarations to control shift registers
const int s1_clock = 0;
const int s1_latch = 1;
const int s1_data = 2;
const int s2_clock = 3;
const int s2_latch = 4;
const int s2_data = 5;
const int s3_clock = 6;
const int s3_latch = 7;
const int s3_data = 8;

//
RF24 radio(10, 9);                  // NRF24L01 (CE,CSN)
RF24Network network(radio);         // include this module in the network
const uint16_t node_acc = 00;
const uint16_t node_signal = 02;
const int data_size = 8;

// char arrays for data storage and processing
char local_signal[data_size] = "DDDDDDDD";
char full_state_list[3 * data_size];
char register_1_data[data_size] = "00000000";
char register_2_data[data_size] = "00000000";
char register_3_data[data_size] = "00000000";
//bytes used for data shifting
byte aspects_sr_1 = 0;
byte aspects_sr_2 = 0;
byte aspects_sr_3 = 0;

//setup run at startup once
void setup() {
  //initialize radio frequency network to communicate with ACC
  SPI.begin();
  radio.begin();
  network.begin(90, node_signal);
  radio.setDataRate(RF24_2MBPS);
  //init pin mode
  pinMode(s1_clock, OUTPUT);
  pinMode(s1_latch, OUTPUT);
  pinMode(s1_data, OUTPUT);
  pinMode(s2_clock, OUTPUT);
  pinMode(s2_latch, OUTPUT);
  pinMode(s1_data, OUTPUT);
  pinMode(s3_clock, OUTPUT);
  pinMode(s3_latch, OUTPUT);
  pinMode(s3_data, OUTPUT);
}

void loop() {
  // connect to RTF network
  network.update();
  //receive aspect to load from ACC via RFC network
  while (network.available()) {
    RF24NetworkHeader master_header;
    char incomming_data[data_size];
    network.read( master_header, &incomming_data, sizeof(incomming_data));
    if (master_header.from_node == node_acc) {
      for (int i = 0; i < sizeof(incomming_data); i++)
        local_signal[i] = incomming_data[i];
    }
  }
  //Incoming data type is R, Y or G aspect type, convert it to int and put it in a 3xdata_size buffer
  decode_aspects_to_register();
  //split the data in to 3 buffers, one for each shift register
  load_registers_simple();
  //clear data in shift registers
  aspects_sr_1 = 0;
  aspects_sr_2 = 0;
  aspects_sr_3 = 0;

  //apply cleared data, allow time for the registers to be loaded
  updateShiftRegisters();
  delay(10);

  //apply new data, allow time for thre registers to be loaded
  load_data_to_byte(aspects_sr_1, register_1_data);
  load_data_to_byte(aspects_sr_2, register_2_data);
  load_data_to_byte(aspects_sr_3, register_3_data);
  updateShiftRegisters();
  delay(10);

}

//according to the shitregisters int values in the buffer, set the byte to be latched to bitwise 1's and 0's
void load_data_to_byte(byte out, char in[]) {
  for (int i = 0; i < 8; i++) {
    if (in[i] == '1')
      bitSet(out, i);
    else
      bitClear(out, i);
  }
}
//bring latch pin to low, put the byte data on the data pin, and pull latch back to high to shift it out
void updateShiftRegisters() {
  digitalWrite(s1_latch, LOW);
  digitalWrite(s2_latch, LOW);
  digitalWrite(s3_latch, LOW);
  shiftOut(s1_data, s1_clock, MSBFIRST, aspects_sr_1);
  shiftOut(s2_data, s2_clock, MSBFIRST, aspects_sr_2);
  shiftOut(s3_data, s3_clock, MSBFIRST, aspects_sr_3);
  digitalWrite(s1_latch, HIGH);
  digitalWrite(s2_latch, HIGH);
  digitalWrite(s3_latch, HIGH);
}


//convert RYG aspects to ints
void decode_aspects_to_register() {
  int j = 0;
  for (int i = 0; i < sizeof(local_signal); i++) {
    switch (local_signal[i]) {
      case 'R':
        full_state_list[j] = 1;
        full_state_list[j + 1] = 0;
        full_state_list[j + 2] = 0;
        break;
      case 'Y':
        full_state_list[j] = 0;
        full_state_list[j + 1] = 1;
        full_state_list[j + 2] = 0;
        break;
      case 'G':
        full_state_list[j] = 0;
        full_state_list[j + 1] = 0;
        full_state_list[j + 2] = 1;
        break;
    }
    j = j + 3;
  }
}

//split the converted int values between the 3 registers
void load_registers_simple() {
  for (int i = 0; i < sizeof(full_state_list); i++) {
    if ( i < 8)
      register_1_data[i] = full_state_list[i];
    if ( i > 7 && i < 16)
      register_2_data[i] = full_state_list[i];
    if (i > 15)
      register_3_data[i] = full_state_list[i];
  }
}

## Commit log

2019-05-24 Initial commit of existing project files
    [central_module.fzz, element_config.txt, sias_example.xlsx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]
2019-05-24 Set led states to LOW at start of each loop.
2019-05-30 added track detection images for documenatation
2019-06-12 Deleted old POC ui desgines, started integrating serrial com.
    [element_config.txt]
2019-06-14 Redone architecture flow and sequence diagrams
2019-06-16 added presentation data, finalized documentation pictures, corrected some bugs in signal and ui code
    [signal_module.ino, ui_test_revised.pde]
2019-06-20 Corrected signal circuit, and UI bug
    [signal_module.fzz]
2019-07-01 fixed some bugs in vacancy
    [vacancy_module.ino]
2019-07-02 Finalized doccument, and code base, cleared up library
    [sias_example.xlsx]
2019-07-02 Resolved some merge conflits in acc and ui
    [acc_module.ino, ui_test_revised.pde]
2019-07-02 minor fixes changes in acc,signal and ui
    [acc_module.ino, signal_module.ino, ui_test_revised.pde]
